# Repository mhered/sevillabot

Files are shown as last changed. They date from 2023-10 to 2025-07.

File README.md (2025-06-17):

# sevillabot
This is the repo for the team **sevillabot** of PiWars 2024 competition:
* [Quick Start Guide](./Quick-start-guide.md)
* [Shortcut Commands](./commands/README.md)
* [Bill of Materials](./BOM.md)
* [Activity Log](./activity_log.md)
* [Raspberry Pi setup (20.04 / Foxy)](./RPi_setup_foxy.md) or alternatively [22.0 / Humble](./RPi_setup_humble.md)
* [Motor wiring](./wiring.md)
* [Soldering Tips](./soldering.md)
* [Gamepad Controls](./gamepad_controls.md)
* [SLAM and Navigation](./SLAM_and_Navigation.md)
* [Line Follower](./Line_follower.md)
* [Simulation in gazebo](Simulation.md)
* [Inertia Properties](./inertial/Inertial.md) and [Center of Mass](./inertial/Weighing.md) estimation
* [Troubleshooting](Troubleshooting.md)
* [WIP](./WIP/) (some unfinished projects with improvements for next version of sevillabot):
  * [Menu](./WIP/menu/README.md): Adding an onboard interface
  * [RPi_zero](./WIP/RPi_zero/): moving from the RPi 4B to the RPi Zero 2 W
  * [IMU](./WIP/IMU/README.md): adding an IMU
* [Where are the large and private files?](./BKP_sevillabot/README.md)

Check out our [blog](https://sevillabot.blog).

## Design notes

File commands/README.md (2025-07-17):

# /commands/README.md
This folder contains bash commands to be used as shortcuts to interact with sevillabot. 

Open a terminal in this folder and launch commands. 

Each command opens a separate terminal.

Warning: this assumes the IP address of the robot has been already named `sevillabot`, see [Troubleshooting.md](../Troubleshooting.md) 

## Shortcuts for frequent remote commands in bot

| Usage | Commands sent to bot over SSH | Comments |
| --- | --- | --- |
| `$ . activate_bot.bash` | `$ cd ~/robot_ws`<br />`$ source install/setup.bash`<br />`$ ros2 launch sevillabot launch_robot.launch.py` | Spawns the robot. Sources ROS2 in the workspace then runs launch file that spawns the robot, launches twist_mux and joystick. |
| `$ . shutdown_bot.bash` | `$ sudo shutdown -h now` | Shuts down the RPi |
| `$ . miniterm.bash` | `$ miniterm` | Launches miniterm |
| `$ . camera.bash` | `$ cd ~/robot_ws`<br />`$ source install/setup.bash`<br />` $ ros2 launch sevillabot camera.launch.py` | Launches camera node |
| `$ . lidar.bash` | `$ cd ~/robot_ws`<br />`$ source install/setup.bash`<br />` $ ros2 launch sevillabot camera.launch.py` | Launches lidar node |

## Shortcuts for frequent commands in PC

| Usage | Commands executed in PC | Comments |
| --- | --- | --- |
| `$ . RVIZ.bash` | `$ rviz2 -d ~/dev_ws/src/sevillabot/config/bot_with_sensors.rviz` | Launches RVIZ with config file to view Lidar |
| `$ . view_image.bash` | `$ cd ~/dev_ws`<br />`$ source install/setup.bash`<br />` $ ros2 launch sevillabot camera.launch.py` | Launches RQT Image viewer |

## Sources

Inspired on this article: https://malcontentcomics.com/systemsboy/2006/07/send-remote-commands-via-ssh.html 
Check out this one too if need to send variables: https://malcontentcomics.com/systemsboy/2006/11/using-ssh-to-send-variables-in-scripts.html

Check this article for ways to launch several terminals or tabs with different titles: https://www.baeldung.com/linux/gui-open-terminals-run-commands

Check this article for ways to concatenate commands: https://unix.stackexchange.com/questions/159489/is-there-a-difference-between-and-and

Check this one for ways to avoid writing the password (e.g. for sudo commands?): [How to automate SSH login with password?](https://serverfault.com/questions/241588/how-to-automate-ssh-login-with-password)

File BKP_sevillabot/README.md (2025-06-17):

# README.md

A private backup of the following large and/or private files of the `sevillabot` project is uploaded to Dropbox:

* `Arduino/` - folder containing a backup of all Arduino `.ino` files in the white LG gram laptop (`gram` or Eve), just in case I forgot to save them in the repo (final ones should be in `code/` folder )
* `CAD`/ - folder containing the original CAD design of `sevillabot`, including FreeCAD files (all versions up to piwars and after, animated mechanisms, STL exports for 3D printing, etc), mega4 design uploaded to GrabCAD, all CAD files downloaded

* `firmware_update/` - folder with the files needed to manually fix ubuntu Mate install in the RPi

* `SD_images/` folder contains images of the SD card in sevillabot, one with a clean ubuntu 20.04 + ROS foxy and the one with all software loaded, as used during the competition in piwars2024

* `secrets.md` - login/pwd of sevillabot blog, email and twitter, wordpress recovery key, etc

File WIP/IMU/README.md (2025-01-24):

# Playing with an IMU

## Sources

- [Arduino Guide for MPU-6050 Accelerometer and Gyroscope | Random Nerd Tutorials](https://randomnerdtutorials.com/arduino-mpu-6050-accelerometer-gyroscope/)

A basic tutorial to get started with the MPU-6050 IMU and Arduino. Describes connections, provides Arduino code to get readings of accelerations and temperature

- [GitHub - hiwad-aziz/ros2_mpu6050_driver: A ROS2 package that interfaces with an MPU6050 sensor over I2C.](https://github.com/hiwad-aziz/ros2_mpu6050_driver)

A ROS2 driver for MPU-6050 IMU. I arrived originally to the fork by JosefGst, but there are plenty more and the one by hiwad-aziz seems to be the original one,. Explore the [forks](https://github.com/hiwad-aziz/ros2_mpu6050_driver/forks) to look for recently active ones. Zerobotics seems linked to Enzo Ghisoni

- [@ros2jsguy/mpu6050-motion-data - npm](https://www.npmjs.com/package/@ros2jsguy/mpu6050-motion-data/v/0.2.0)

Another MPU-6050 driver writtn in Typescrit 

- [Lessons learned while working with IMU Sensor, ROS2 and Raspberry Pi | by RoboFoundry | Medium](https://robofoundry.medium.com/lessons-learned-while-working-with-imu-sensor-ros2-and-raspberry-pi-a4fec18a7c7)

Comparison MPU6050 vs BNO055 (with magnetometer), calibration. There are more articles in the series.

Series of 3 Youtube vides by NeroCode. I saved local copies with subtitles to watch offline in [./videos_IMU_local](./videos_IMU_local):

- [(222) Control Robot Móvil Diferencial con ROS con Odometría | DESDE CERO | Parte 1 - YouTube](https://www.youtube.com/watch?v=1Ch-gtxvxyA)
- [(222) Cómo publicar datos de IMU MPU6050 usando ROS | Parte 2 - YouTube](https://www.youtube.com/watch?v=TaHY4OYBNwc&t=18s)
- [(222) Fusión de datos de IMU y Odometría de encoders mediante ROBOT_LOCALIZATION en ROS | Parte 3 - YouTube](https://www.youtube.com/watch?v=OopVfPZ2_ig)

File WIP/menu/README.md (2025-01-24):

# README.md

Miniproject to create a minimal interface aboard the robot.

Components:

* KY40 rotary encoder with switch
* SS1306 0.96" OLED display screen
* 3D printed parts

## 3D printed parts

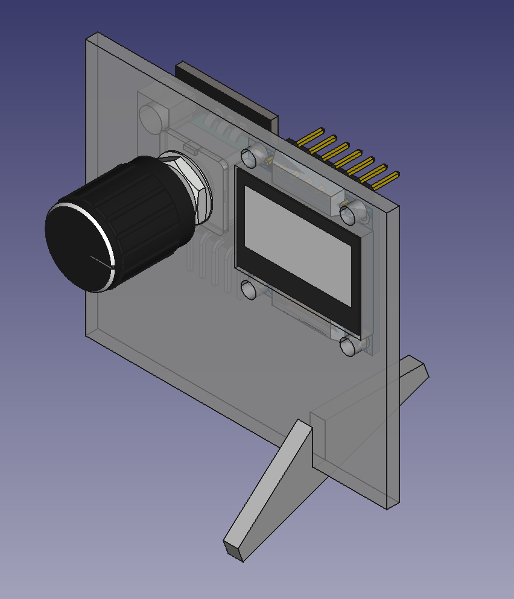
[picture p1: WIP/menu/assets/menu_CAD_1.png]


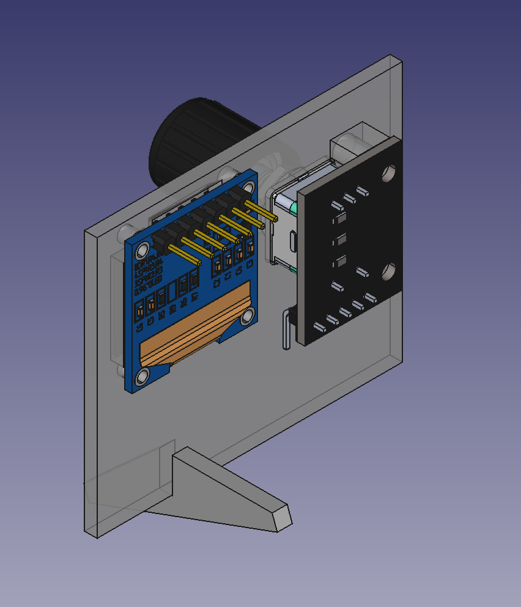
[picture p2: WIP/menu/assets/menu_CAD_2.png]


I downloaded CAD files of the components to aid the design, then fine tuned with physical measurements. Notes about the downloaded CAD files:

- `rotary-encoder-with-knop-1.snapshot.1`: downloaded as SLDPRT, converted to STEP using OnShape, OK!
- `oled-0-96-display-1.snapshot.1`: downloaded as STEP and OK(-ish, dimensions are a bit off and 6 pins instead of 4)
- `ky-040-rotary-encoder-1.snapshot.1`: downloaded as SLDPRT, converted to STL in AnyConv: KO, wrong scale!!
- `display-oled-ssd1306-de-0-96-1.snapshot.6`: downloaded as STEP but KO, dimensions not fitting part

Note: Some options for converting SLDPRT for free without SolidWorks:

* [AnyConv](https://anyconv.com/) but rather unreliable: scale not respected, or failure to convert 
* [ConvertCADFiles](https://convertcadfiles.com/): one free trial, afterwards pay per conversion
* Create account in [OnShape](https://cad.onshape.com/) (with SPAM user), open file then export as STL or STEP
* Not tested: [download eDrawing](https://www.solidworks.com/support/free-downloads) (for Windows)

## Arduino

### Wiring

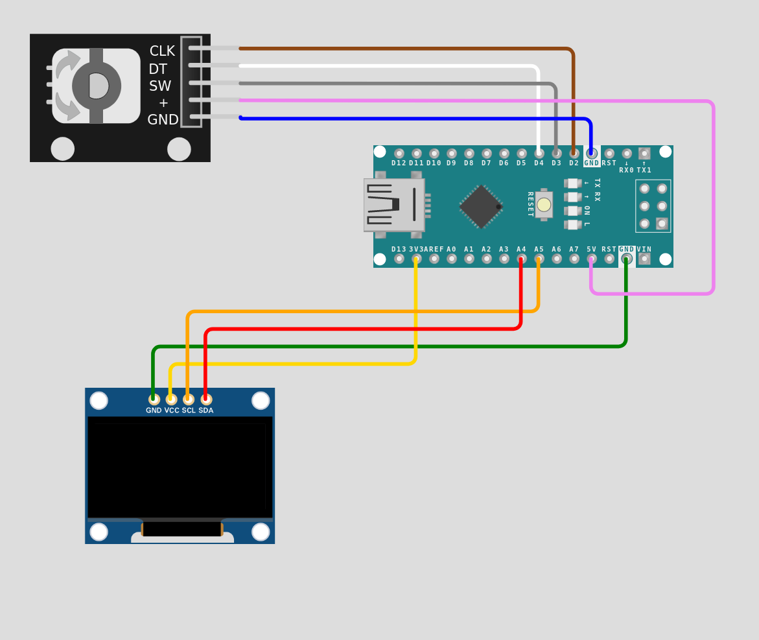
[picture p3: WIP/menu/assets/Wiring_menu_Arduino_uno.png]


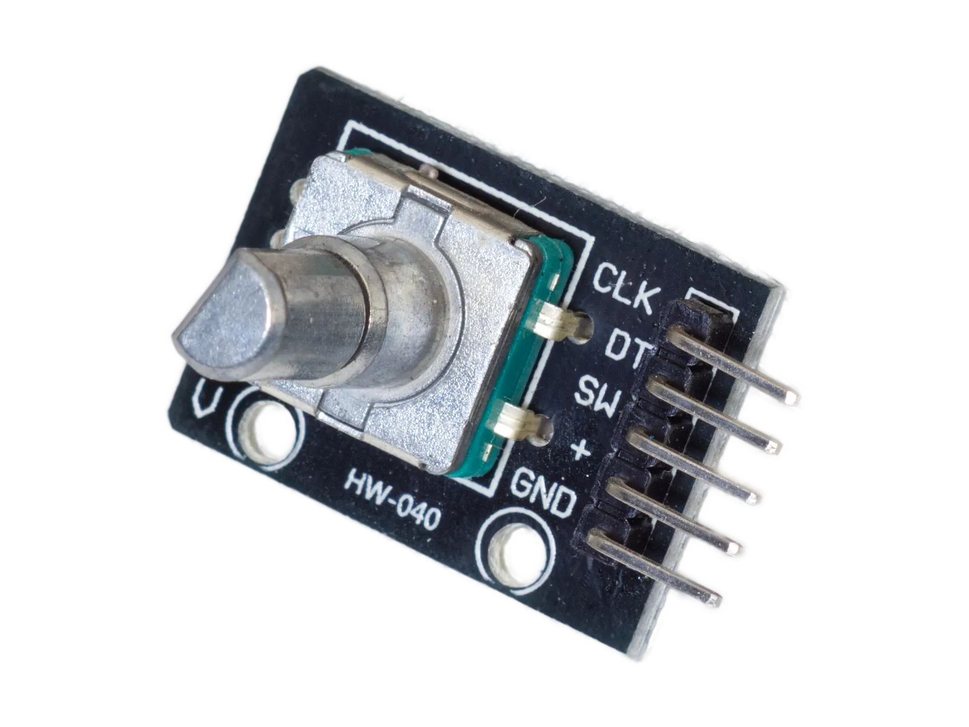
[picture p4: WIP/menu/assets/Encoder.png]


| KY-40 pin | Cable  | Arduino pin |
| --- | --- | --- |
| GND | blue | GND |
| + | purple | 5V |
| SW | grey | D3 |
| DT | white  | D4 |
| CLK | brown  | D2 |

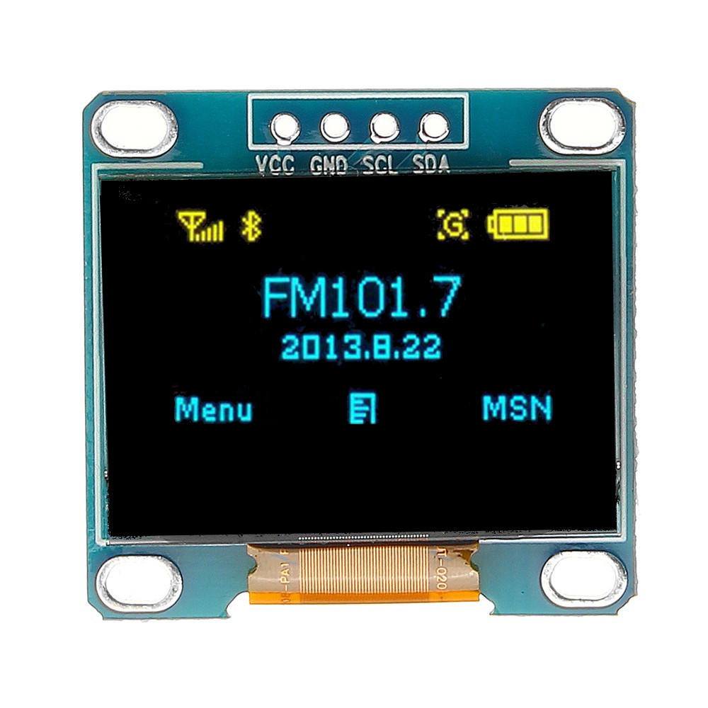
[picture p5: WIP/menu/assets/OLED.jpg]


| OLED pin | Cable  | Arduino pin |
| --- | --- | --- |
| GND | green  | GND |
| VCC | yellow | 3V3 |
| SCL | orange | A5 / SCL |
| SDA | red | A4 / SDA |

### Programming

#### Sources

* Inspired on the [video tutorial by upir ](https://www.youtube.com/watch?v=HVHVkKt-ldc) and [companion code](https://github.com/upiir/arduino_oled_menu/tree/main) for a beautiful menu design with icons for the OLED display. Note this code controls the menu using 3 push buttons. 

* I used ideas from this [video tutorial by LaBuhardillaDelLoco](https://youtu.be/cWgWvNhWg-A) and the [GFX library documentation](https://learn.adafruit.com/adafruit-gfx-graphics-library?view=all) to migrate to the Adafruit GFX and SSD1306 libraries for the OLED display,  instead of `u8g` (it was not working, although in hindsight it was probably due to wiring errors)

* Used ideas from this [video tutorial by Yvan from brainy-bits](https://www.youtube.com/watch?v=cYCTMdUi8P0 ) and its [companion blog post with code](https://www.brainy-bits.com/post/best-code-to-use-with-a-ky-040-rotary-encoder-let-s-find-out) on how to control a rotary encoder (with debouncing) to use it as input method
* Another [simpler menu with rotary encoder tutorial](https://www.youtube.com/watch?v=vHRyj3e3ZTU), which I didn't really use

* Created my own graphics online: used [Pixilart](https://www.pixilart.com/) which is super simple instead of [Photopea](https://www.photopea.com/) which is way more complex

* Convert images into C code arrays using online tool [image2cpp](http://javl.github.io/image2cpp/) 

* Test the sketch online using [WOKWI online emulator](https://wokwi.com/projects/397015999090347009) although it was not very practical with the OLED, had a tendency to trigger unexplained build errors when tweaking the appearance.

### Arduino sketch

Notes:

* Modified the Encoder code so it only registers clockwise or counterclockwise input when a full notch is moved (i.e. the knob fall in a stable position). Original code counted also halfway movements. 
* Encapsulated the code to control the encoder in a custom `Encoder` class. To include a class in arduino: add `#include "src/Encoder.h"` and put `Encoder.h` and `Encoder.cpp` files in a `/src/` subfolder below the location of the main `.ino` file, see [here](https://forum.arduino.cc/t/how-do-i-include-a-library-in-a-sketch-directory/1079812)
* I simplified a lot the code for the menu

### Issues / To Do

- [ ] The debouncing should not work because the wait time is almost 0! It was working when the only action is to print the command via serial (e.g. see `rotary_encoder_control_class.ino`)
- [ ] When the menu code is added to the mix, it fails sometimes to detect accurately the Encoder input, and behaves a bit erratically (e.g does not react or moves to the wrong selection ). Why?

- [ ] Encapsulate menu in a class

## Raspberry pi

Next step translate to use directly with RPi

See e.g. [this tutorial by Computadores y Sensores](https://www.youtube.com/watch?v=n0dHQSTSilM) which uses raspiOS, python and LUMA library. There are plenty of interesting examples reading info from the RPi system (e.g. date and time, network usage, temperature? )

#### Wiring

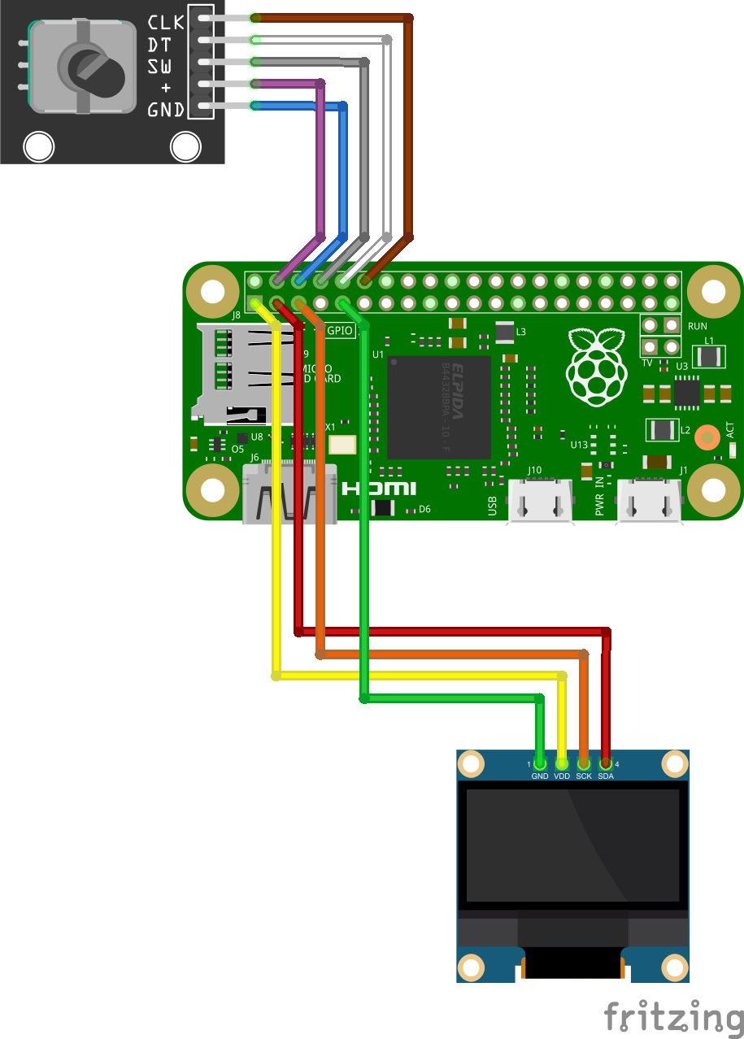
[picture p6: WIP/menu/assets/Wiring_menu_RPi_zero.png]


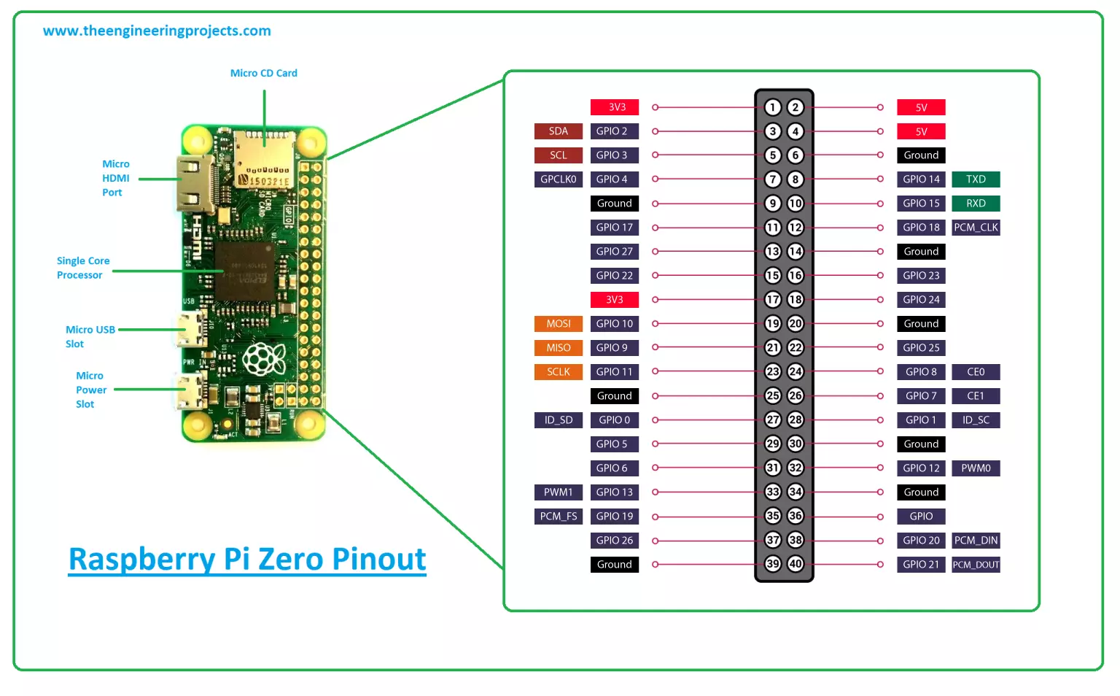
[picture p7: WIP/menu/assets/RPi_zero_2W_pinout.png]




| KY-40 pin | Cable  | RPi pin |
| --- | --- | --- |
| GND | blue | GND / #6 |
| + | purple | 5V / #4 |
| SW | grey | GPIO14 / #8  |
| DT | white  | GPIO15 / #10 |
| CLK | brown  | GPIO18 / #12 |



| OLED pin | Cable  | RPi pin |
| --- | --- | --- |
| GND | green  | GND / #9 |
| VCC | yellow | 3V3 / #1 |
| SCL | orange | GPIO 3 / SCL / #5 |
| SDA | red | GPIO 2 / SDA / #3 |

### Setup

I2C requires activation in Raspi, see this discussion: https://askubuntu.com/questions/1273700/enable-spi-and-i2c-on-ubuntu-20-04-raspberry-piNo but there is no need in ubuntu.

Install i2c-tools and check I2C devices are detected: 

```bash
sudo apt install i2c-tools
i2cdetect -y 1
     0  1  2  3  4  5  6  7  8  9  a  b  c  d  e  f
00:          03 -- -- -- -- -- -- -- -- -- -- -- -- 
10: -- -- -- -- -- -- -- -- -- -- -- -- -- -- -- -- 
20: -- -- -- -- -- -- -- -- -- -- -- -- -- -- -- -- 
30: -- -- -- -- -- -- -- -- -- -- -- -- -- -- -- -- 
40: -- -- -- -- -- -- -- -- -- -- -- -- -- -- -- -- 
50: -- -- -- -- -- -- -- -- -- -- -- -- -- -- -- -- 
60: -- -- -- -- -- -- -- -- -- -- -- -- -- -- -- -- 
70: -- -- -- -- -- -- -- --      
```

Install dependencies:

```bash
sudo apt-get install python3-dev python3-rpi.gpio
sudo apt install python3-pip
sudo pip3 install adafruit-circuitpython-ssd1306
```

Create a sample program

```python
from board import SCL, SDA
import busio
import adafruit_ssd1306

i2c =busio.I2C(SCL, SDA)

# create calss and define screen size

display = adafruit_ssd1306.SSD1306_I2C(128, 64, i2c)

#clear screeeb

display.fill(0)
display.show()

# define 1 pixel at the origin 0,0
display.pixel(0,0,1)

# define 1 pixel at center point
display.pixel(64,32,1)

# define 1 pixel at the opposite corner
display.pixel(127,63,1)

display.show()
```

It works!

#### Programming

#### Issues / To Do

- [ ] ssh onto the zero via USB: see this tutorial https://johnnymatthews.dev/blog/2021-02-06-connect-to-raspberry-pi-zero-over-usb-on-ubuntu/

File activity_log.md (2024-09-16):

# Made a blog in BlueHost

See secrets.md in local

# Made some logos

BrandCrowd (spam.mhered): https://www.brandcrowd.com/maker/shortlist/718945c4-b511-4b5e-aa74-6c4dfafddd57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

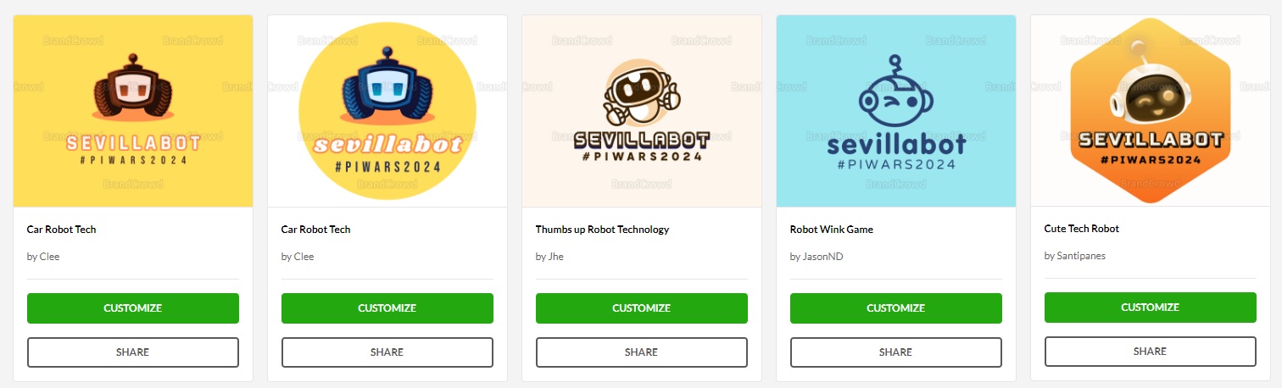
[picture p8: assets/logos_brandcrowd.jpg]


Looka.com: seems I didn't sign up and got assigned user: looka-ref-user-name-4GAHPhyn9S. Difficult to change the logo (need to scroll endlessly) 

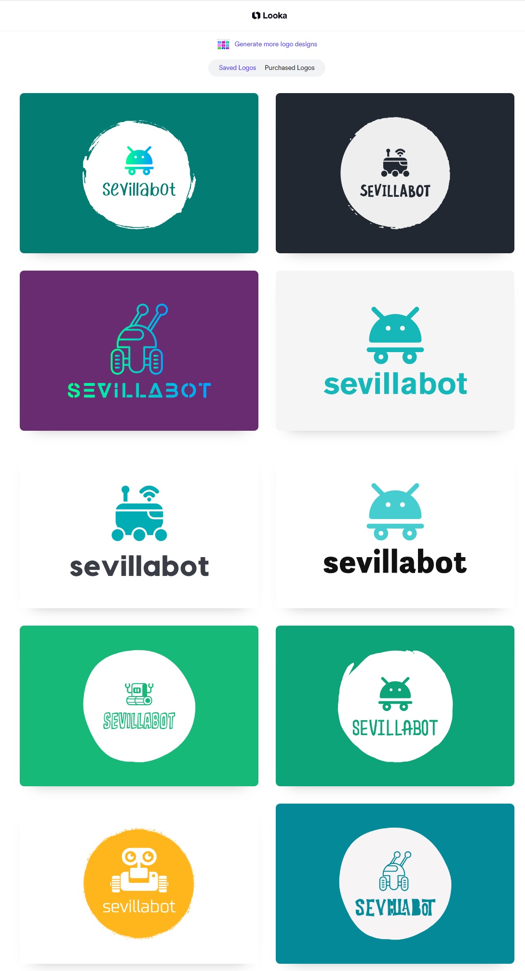
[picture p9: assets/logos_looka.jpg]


Temporary logo I chose for the blog:

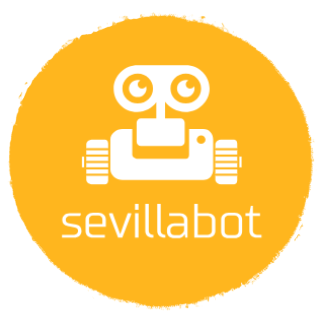
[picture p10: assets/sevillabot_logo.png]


# Ordered some items

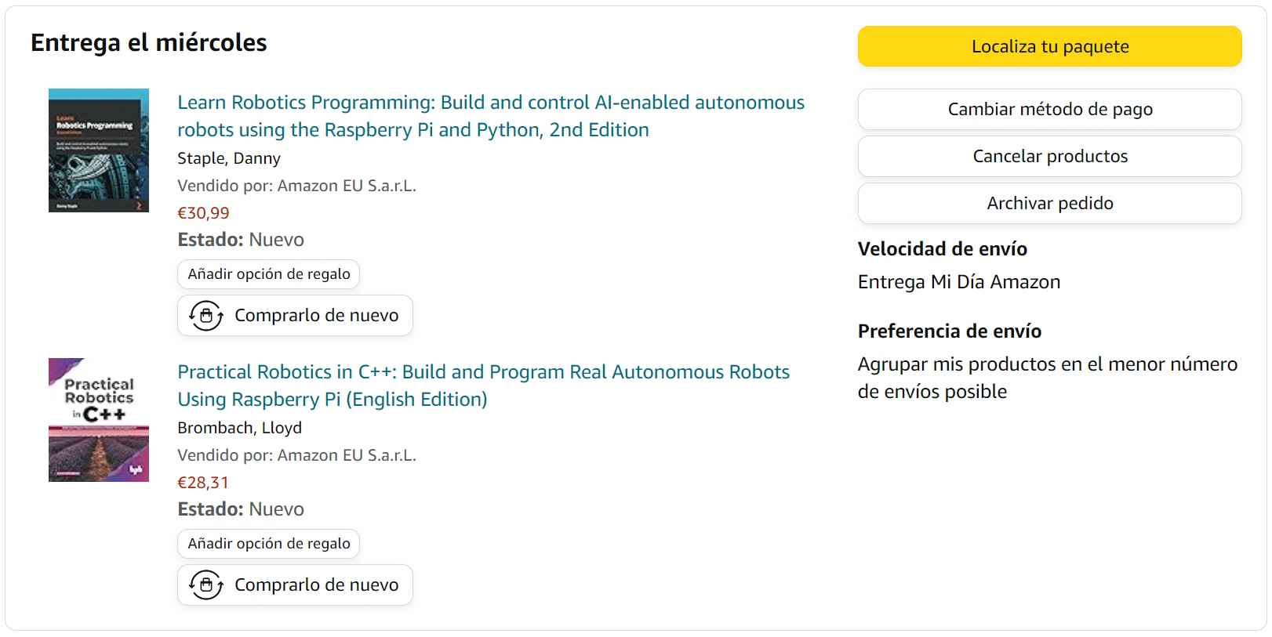
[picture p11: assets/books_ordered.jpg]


* Practical Robotics in C++ by Lloyd Brombach

* Learn Robotics Programming 2nd Ed by Danny Staple
* A Raspberry Pi 5
* 2x microUSB flat cables from Aliexpress (with a second account that uses Apple OAuth)
* Motors (x4), battery (x2), Arduino Nano (x3), and Buck converter (x3) all of them with some spares, from Amazon.

# Gathered references

Robofoundry resources: https://robofoundry.medium.com/

Checked out Simon robot: 

* https://esimonsite.com/proyectos/mini_robot/
* STEP file: https://github.com/simonllopez/mini_robot_hw/blob/c72156409fd8e69483608780fe5bce98770d15b5/Ensamblaje_Base_2023.step

# Notes on #piwars

38 Adults & Mixed teams will compete on 21st April in 3 categories: Beginner, Intermediate and Professional. **sevillabot** will compete in the category Beginner.

We make three commitments: 

- to build a robot to compete on the appropriate competition day.
- to provide regular updates, when requested, to assure that we are on track to complete our robot build and testing by the competition date. The organization will be setting deadlines for replies to ensure that spaces are not wasted, so **it is vital to respond to update requests** .
- to respond to (or acknowledge) all communications in a timely manner.

There is a fee of 20 GBP per team.

All teams must send at least one participant to the physical event in Cambridge. The maximum recommended team size is 10 people. The organization will ask how many members are actually attending to assign a suitable workroom onsite. All teams must have or be accompanied by a responsible adult. 

# Safety rules 

* In the workrooms all robots must remain powered down or ‘on blocks’ to prevent any remote control conflicts or autonomous mistakes may cause damage.
* Robots must not (intentionally) emit smoke or flames.
* No soldering within the building. Soldering is acceptable outside the building with a **battery-powered soldering iron**, taking care that no smoke enters the building and triggers the smoke detectors. 

# Robot rules

## One single robot

We are permitted to enter **one single robot** to the competition. This robot must handle all of the challenges. We are not permitted to *swap out* the entire robot at any time. It may have attachments, and we are permitted to exchange *parts* of our robot to compete in the different challenges (e.g. motors and wheels) but it must remain fundamentally the *same* robot: When adding attachments, the basic chassis, Raspberry Pi and controller arrangement must remain the same.

## With an official Raspberry Pi at the Core

We may use multiple Pis (Pi, Zero, Pico) and other boards (e.g. Arduinos, micro:bits, even non-official RP2040-derived boards, or other) BUT **an official Raspberry Pi board must be in overall/central control of your robot as the primary/core processor**. 

Additional pieces of equipment e.g. a games controller, a laptop, mobile phone or tablet may be used to control the robot, but **must not be physically attached when competing on the courses**.

## Battery-powered

All robots must be powered by batteries and must operate without being tethered to a static mains electricity power source.

Mains power may be used for recharging battery packs.

If LiPo batteries are used, **any charging must supervised and be done inside a fire-proof bag or box**

## Only some configurations are allowed

No airborne robots are permitted, e.g. drones.

Walking and self-balancing robots are permitted.

Hovercraft-style robots are allowed *provided that any fans are enclosed safely*.

## And robot dimensions are constrained

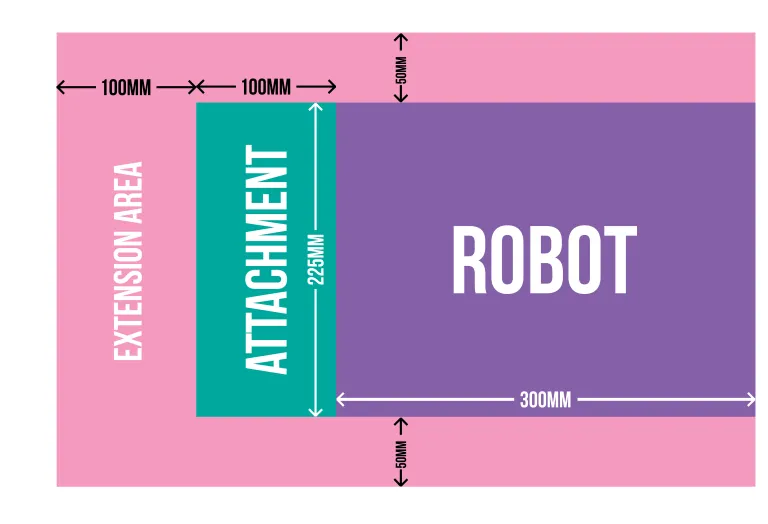
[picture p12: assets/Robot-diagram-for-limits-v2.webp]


### Main chassis

The main chassis (including wheels and any protrusions that form part of the main robot) of competing robots must fit within a 225mm width x 300mm length x 370mm height box (purple area)

### Attachments

Attachments may be added to the robot for specific challenges. Any attachment can add additional length of 100mm and height of 80mm (as in the green area in the diagram above) such that, when the attachment is at rest there is no additional width, maximum length must be no more than 400mm, the maximum height must be no more than 450mm.

An attachment may be *animated* in some way such that it extends beyond the boundaries above into the “extension area”. However, the attachment must stay within a box 325mm wide by 500mm length (this is shown as the pink area above).

## Our thoughts

The basic architecture of our current robot is in line with the rules, but we need to think about changing the chassis because the wheels are too wide apart and the camera protrudes too much at the front (although the camera could pass as an attachment maybe?).

Will need to adapt the dimensions of the current robot: 34cm long (ko by 4cm, would need to move front camera) x 27 cm wide (ko by 5.5cm, could fix moving wheels inwards because bottom width is 14cm and wheel width is 3cm, leaves 1cm clearance in each side and some to spare) x 24 cm high (ok)

Other changes: 

* should remove large screen (heavy and hungry)
* Castor wheels are not recommended. Consider 4WD mecanum? How to program mecanum wheels: https://www.youtube.com/watch?v=gnSW2QpkGXQ

# The Challenges

Each challenge can earn points that contribute to an overall score. None are mandatory but no points can be earned from challenges not entered.

## [Lava Palava](https://piwars.org/2024-disaster-zone/challenges/lava-palava/) - Escape the volcanic eruption

This challenge is autonomous-only: the Raspberry Pi will control the robot by itself for the entire duration of the challenge without interference from the operator, except for a button press to initiate movement and another, if necessary, to stop movement.

This will require a line-following algorithm. I think there are specific line-detection sensors, otherwise I could use a camera. Potentially I could use a Lidar to stay away from the walls.

4/1 We bought a line sensor, built a support and tested the sensor on a black line over white background. It was not very robust, perhaps related to calibration with direct light and shadows? We need to modify the code to detect a white line over black background. Also, need to add a PID, but I need a working robot base to calibrate the gains and test it!

1/2 checking dimensions to mock-up the arena for testing: 7m long course, 570mm long by 53mm high speed bump, section is channel 550mm wide with 70mm high walls (even in speed bump), painted black with 19mm wide white centre line. There are 2 turns, looking at the sketch the turns are approx 780mm long at 45 degrees. Robot must cross finish line. Need start/stop button. Retrieve manually from end of course. 3 runs. Apparently in the documentation: https://www.pololu.com/docs/0J18/17 there is a `read_line_white()` function.

## [Eco-Disaster](https://piwars.org/2024-disaster-zone/challenges/eco-disaster/)- Sort the barrels of toxic waste!

### Challenge description

This challenge can be driven autonomously *or* by remote control. The points available are weighted so autonomous robots can earn more points.

### Our thoughts

1/1 Finished the first working prototype of a beautiful clamp actuated by a stepper motor. Need to have a working base robot to be able to test it.

## [Escape Route](https://piwars.org/2024-disaster-zone/challenges/escape-route/) - Navigate the blind maze to find your way out!

### Challenge description

The arena for the maze is made of a by a 2m by 3m area surrounded by a 119mm high walls, all painted in matte black. There are 3 colored blocks (red, green, blue) are placed as obstacles in any one of six predefined configurations, unknown in advance.

There are three ways to compete in this challenge (The points available are weighted so autonomous robots can earn more points):

* **Fully autonomous**: The team has 1' to calibrate the vision system then can only press start and stop.
* **Blind remote control**: Teleoperated via sensora on the robot and a screen for the driver.
* **Call and response**: With a team member looking at the maze and giving instructions to a driver who cannot see the maze

### Our thoughts

I am thinking going for blind remote control if I can position the lidar below 119mm. For this one I need to build a replica of the maze and practice a lot!

## [Minesweeper](https://piwars.org/2024-disaster-zone/challenges/minesweeper/) -  Find and defuse the bombs!

### Challenge description

Arena: 1.6 by 1.6m area surrounded by 30cm tall black walls. The floor is made of 4x4 squares of white opaque perspex.

A single, random square will be lit up in red. The robot must visit the  square in question and stop, motionless for 1 second with some part of  the robot over the square. The light goes off and another random tile lights up up to 20 times.

Autonomous teams will have 1' to calibrate the vision system.

This challenge can be driven autonomously or by remote control. The points available are weighted so autonomous robots can earn more points.

### Our thoughts

I can imagine some vision system based on a top mounted camera, then a routine that turns the robot until the light is in front of the robot, then moves towards it, stops when it is on top of it, then waits 1", then repeats when a .

Mocking somewhere to test to fine tune (field of view, detecting light, when to stop etc) may be difficult though. I think we may compete here with remote control.

11/12 - check out this very nice blog:https://eastdevonpirates.blogspot.com/2023/12/minesweeper-piwars-2024.html with a discussion.

Found 30cm 130 degree convex mirrors in Amazon for 30€. Made some calculations and with a picamera (75degrees angle of view) placed at 10cm from the floor looking upwards, the convex mirror placed 20cm above the camera facing downwards I could monitor a circle 154cm in diameter. But the mirror weighs 1kg...

## [The Zombie Apocalypse](https://piwars.org/2024-disaster-zone/challenges/zombies/) - Shoot the undead!

### Challenge description

The robot is placed 1- 1.5m away from a tower with 3 levels: ground, middle and top floor up to 60cm above ground. The aim is to hit card-sized targets (62mm by 88mm) using balls or Nerf projectiles.

This challenge can be driven autonomously *or* by remote control. The points available are weighted so autonomous robots can earn more points.

However, as there uncertainty about the exact distance and the geometry of the tower, we don't know really how to identify the targets automatically. By color? Some specific design? Generally, we have questions about this challenge. What are targets in the "compound"? 

### Our thoughts

Today (19/10) I bought a [laser pointer]() and a [Nerf](). I am thinking about attaching the nerf and adding some servos to aim up and down, pull the trigger of the Nerf and reload it. Also I could imagine some way of auto aiming by detecting the laser with a camera, but I don't really know how to choose the target automatically.

11/12 - check out new information released in the discord and the official website with details of the arena and the design of the zombies

24/1 We made a beautiful prototype gun that employs 3D printed structural parts, a car door lock actuator to pull the trigger and a stepper motor to aim the gun in pitch. In order to increase precision and reduce torque, we used a pulley system with a small gear and a large gear.

Observations from the first test of the prototype in a mock-up arena for the zombie challenge:

* The completed gun assembly fits within 400mm long x 200mm wide x 200 mm high box, which should be ok.
* We need to balance the gun: the axle is too far forward. Since there is not much room to move the axis backwards, this can be compensated instead adding weight at the front of the gun (two tape rolls on top of the laser pointer made the trick). Without this, the stepper motor does not really have enough torque to lower the gun and aim lower
* There is not enough clearance between the trigger mechanism and the supports or the robot base for the pitch angle range to reach the higher positions at the top of the 60cm high target area, specially from the closest 1m distance. We need to redesign the supports to make them at least 40mm higher and give them more angle so the attachment of the supports to the robot moves forward at least 30mm. This may cause FreeCAD to break....  
* The pulley system does not appear robust. At times it seems to hesitate or skip teeth, perhaps the stepper is lacking torque and/or the belt is not tight enough. Although applying the stepper directly to the axis may provide sufficient precision, this requires more torque... maybe try the NEMA stepper without the pulley system?

28/1 - Progress:

* Realised it may be sufficient to move supports apart so they don't clash with the trigger mechanism.
* Modified supports: 30 mm higher, replaced clamp with clip-on system to secure bearing in place. Issue: Pending testing, RH support seems flimsy and may require reinforcement.
* Modified 3D printed parts `gun_holder` to move axle backwards, `trigger_support` to clear the battery compartment, plus made RH and LH to make assembly narrower
* Realised jammings can be solved from the cartridge compartment, no need to access the other door
* Installed all elements temporarily on the robot base (battery, fuse, power rail, arduino, motor driver, relay, door lock actuator) 
* Implemented basic keyboard control to aim the gun, toggle the laser and to fire the trigger.  Keyboard control works with python script `command_gun.py` running in the computer. Issues: `keyboard` library requires `sudo`, need to manually set in the code the port in which Arduino is connected. One keyboard press some times fires several shots in quick succession. 
* Tested NEMA17 motor with L298N driver and arduino. May not have enough resolution: 200 steps means 1.8 degrees resolution means 47mm steps at 1.5m! 

## [Pi Noon - The Hindenburg Disaster](https://piwars.org/2024-disaster-zone/challenges/pi-noon/) - Defend your balloon from an explosive end!

One (or more) members of the team will control the robot via wireless controller(s). This challenge *could* be tackled autonomously for the laughs, without extra points.

24/1 still waiting for the block

29/1 Delivery failed because 5€ worth of taxes were due... Will need to pick it up from the post office.

## [The Temple of Doom](https://piwars.org/2024-disaster-zone/challenges/temple-of-doom/) - Go on an adventure and tackle the obstacles in your way!

This is a remote-controlled challenge to test the agility of our robot and our driving skills. The obstacle course will only be revealed on the day of the competition, so it is important to watch the competition on Saturday. 

Not a lot of information, we just know that the course contains "several fiendish traps, snags and puzzles", and some recommendations from the organization of robot features that may help: 

* low center of gravity
* good ground clearance
* good grip
* power to drive up slopes

All obstacles **must** be *attempted* first, then we may skip them (but no points for skipped obstacles). We have up to **three attemps** at the challenge within the 5' time limit.

### Ideas to improve wheel grip

* Add weight to the robot
* moving the CoG above the wheel axis (away from the caster)
* Add rubber additive / liquid latex?

# Opportunities for more points

- [**Blogging Challenge**](https://piwars.org/2024-disaster-zone/challenges/blogging/) – Describe our **pre-event** exploits in words, videos and/or photographs. [See some hints here](https://piwars.org/blogging-challenge-guidelines/). Up to 1400 points per robot.
- [**Technical & Artistic Merit**](https://piwars.org/2024-disaster-zone/challenges/technical-and-artistic-merit/) – **record a video up to 5' in length** and **submit it ahead of the competition** to document the robot's Technical Merit (features, build quality and other technical aspects) and the design and artistic features (Artistic Merit). Videos will be scored by expert judges ahead of the competition. Up to 2800 points per robot.
- **Most Disastrous Robot Special Award** – to the robot that has the design most influenced by the Disaster theme (natural, man-made, movie-style disasters, or a combination, responses to disaster such as rescue vehicles etc. Up to 700 points per robot.

## Resources

* Cool Piwars blogroll: https://philipmcgaw.com/piwars-blogroll/

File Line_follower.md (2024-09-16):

# Line Follower

## Setup

### Custom messages

1. Create a `/msg` folder and declare custom message `TimestampedData.msg`

```
int64 timestamp
int32 data
```

2. modify `CMakeLists.txt`:

```python
...
# find dependencies
find_package(rosidl_default_generators REQUIRED)

# Declare ROS2 interface files
rosidl_generate_interfaces(${PROJECT_NAME}
  msg/TimestampedData.msg
  DEPENDENCIES std_msgs
)

# Export dependencies
ament_export_dependencies(rosidl_default_runtime)
...
```

3. modify `package.xml`

```xml
  <buildtool_depend>rosidl_default_generators</buildtool_depend>
  ...
  <exec_depend>rosidl_default_runtime</exec_depend>
  <member_of_group>rosidl_interface_packages</member_of_group>

```

4. compile, source and check it is available

```bash
$ colcon build --symlink-install
$ source install/setup.bash
$ ros2 interface list | grep sevillabot
    sevillabot/msg/TimestampedData
```

Note: For some reason when the node is called from normal terminal it freezes and publishes always the same value:

```bash
$ ros2 run sevillabot line_follower_publisher.py
$ # or
$ python3 ./src/sevillabot/my_scripts/line_follower_publisher.py
```

I need to call it from vs_code terminal, and after that it runs well... why? 

## Quick Start Guide for Gazebo

Plug the line follower add-on

Launch  publisher, PID, gazebo, RVIZ and twist_mux

```bash
(in VSCODE Terminal!!)$ ros2 run sevillabot line_follower_publisher.py 

(PC T1)$ ros2 run sevillabot pid.py 

(PC T2)$ ros2 launch sevillabot launch_sim.launch.py world:=~/dev_ws/src/sevillabot/worlds/obstacles.world

(PC T3)$ rviz2 -d ~/dev_ws/src/sevillabot/config/slam_gazebo.rviz

(PC T4)$ ros2 run twist_mux twist_mux --ros-args --params-file ~/dev_ws/src/sevillabot/config/twist_mux.yaml -r cmd_vel_out:=diff_cont/cmd_vel_unstamped

```

When moving the sensor away from the line the robot turns to counter the error!!

## Quick Start Guide Robot

### Launch the robot

Currently requires three calls, each of which requires to ssh into sevillabot, `cd ~/robot_ws`, `source install/setup.bash`. I should combine these three in a single launch file.

```bash
(bot T1)$ ros2 launch sevillabot launch_robot.launch.py # launch robot

(bot T2)$ ros2 launch sevillabot joystick.launch.py # launch gamepad

(bot T3)$ ros2 run twist_mux twist_mux --ros-args --params-file ~/robot_ws/src/sevillabot/config/twist_mux.yaml -r cmd_vel_out:=diff_cont/cmd_vel_unstamped # launch twist_mux
```

After modifying robot_launch, the three calls no longer necessary:

```bash
(bot T1)$ ros2 launch sevillabot launch_robot.launch.py # launch robot, gamepad & twist_mux
```

Equivalent to the shortcut:

```bash
(PC)$ cd sevillabot/commands/
(PC)$ . activate_bot.bash
```

### Launch the subscriber

I don't know yet why the subscriber is not launching properly but found a hack that works:

1. miniterm onto Arduino. Note this triggers calibration (2 solid LED in Arduino) and it takes a little while before it starts publishing data. Move around the sensor in and out the line during the calibration period, otherwise data will not be reliable later. When calibration finishes, LEDs in the Arduino start blinking.

```bash
(bot T4)$ miniterm 

--- Available ports:
---  1: /dev/ttyAMA0         'ttyAMA0'
---  2: /dev/ttyUSB0         'USB2.0-Ser!'
---  3: /dev/ttyUSB1         'USB2.0-Ser!'
--- Enter port index or full name: 3

E:12568	3500 #frozen during calibration
E:12568	3500
E:12568	3500
E:12568	3500
....
E:16367	3500 # then starts transmitting
E:16620	3501
E:16873	3502
E:17127	3498
E:17380	3499
E:17633	3505
```

2. launch the node in another terminal

```bash
(bot T5)$ ros2 run sevillabot line_follower_publisher.py 
```

3. close miniterm in the previous terminal with `CTRL + ]`. This somehow wakes up the node and it starts publishing. 

```bash
(bot T4)$ # exit miniterm with CTRL + ] : hack to get line_follower_publisher.py to publish!!
```

### Launch the PID node

Warning: put the robot on blocks because soon as you launch this node the robot starts moving. 

We can reuse Terminal 4 after closing miniterm

```bash
(PC T4)$ ros2 launch sevillabot pid.launch.py 
```

The advantage of using the launch file instead of running the node directly (`ros2 run sevillabot pid_node.py`) is that the launch file reads the PID gains and linear speed from the YAML file line_follower_pid.yaml. An example that works for speed = 0.1:

```yaml
line_follower_controller:
  ros__parameters:
    Kp: 20.0
    Ki: 0.0
    Kd: 2.0
    linear_vel: 0.1
```

For 0.15:

```yaml
line_follower_controller:
  ros__parameters:
    Kp: 30.0
    Ki: 0.0
    Kd: 3.0
    linear_vel: 0.15
```

You can modify the parameters in the file and relaunch the node without the need for recompiling.

After modifying the distance between wheels the above parameters don't work anymore.

An example that works for speed = 0.1 (with wheels @ 225mm instead of 275)

```yaml
line_follower_controller:
  ros__parameters:
    Kp: 15.0
    Ki: 0.0
    Kd: 0.0
    linear_vel: 0.1
```

## Quick Start Guide Line Follower with shortcuts

```bash
$ . activate_bot.bash # spawn bot
$ . miniterm.bash # launch miniterm
$ . line_sensor.bash # launch line_sensor subscriber. Close miniterm to activate it
$ . pid.bash # launch PID to start moving
```

## To do

- [ ] Understand and fix why the `line_follower_publisher.py` node only works when launched from vs_code terminal (??) -> Seems related to serial communication. Opening and closing miniterm seems to work as well.
- [x] modify `pid_node.py` to read PID constants and linear speed from `line_follower_pid.yaml` -> this will simplify fine tuning Done 11/04/24
- [x] integrate gamepad and twist_mux in the robot launch file `launch_robot.launch.py` -> this will simplify launching! DONE 13/04/24
- [ ] maybe try to integrate also `line_follower_publisher.py` and `pid.py` in a `launch_follower.launch.py`, this will simplify launching, and may fix the issue with serial!

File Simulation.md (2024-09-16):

# Simulation

## Quick start

1. Spawn the robot

```bash
$ cd ~/dev_ws/
$ source install/setup.bash
$ ros2 launch sevillabot rsp.launch.py use_sim_time:=true
```

2. Launch gazebo

```bash
$ cd ~/dev_ws/
$ source install/setup.bash
$ ros2 launch sevillabot launch_sim.launch.py
```

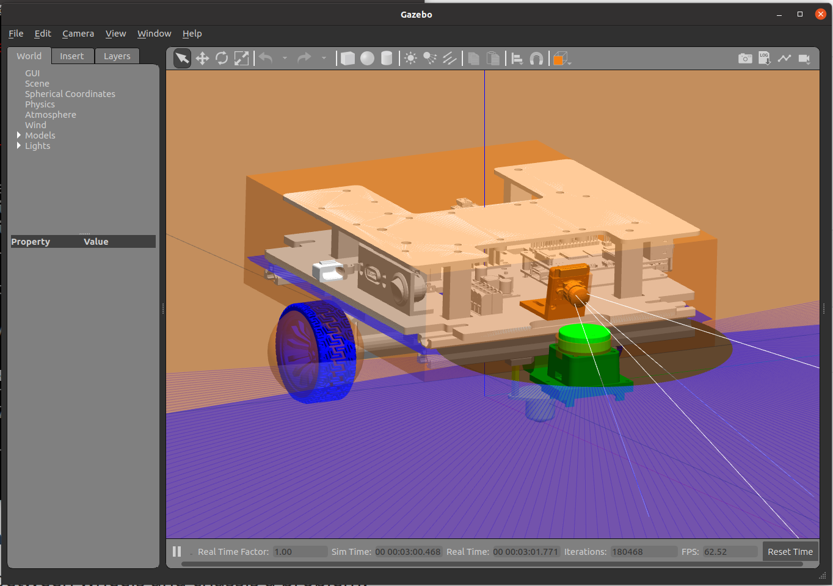
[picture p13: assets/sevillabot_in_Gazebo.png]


3. Display in RVIZ

```bash
$ cd ~/dev_ws/
$ source install/setup.bash
$ ros2 launch sevillabot display.launch.py
```

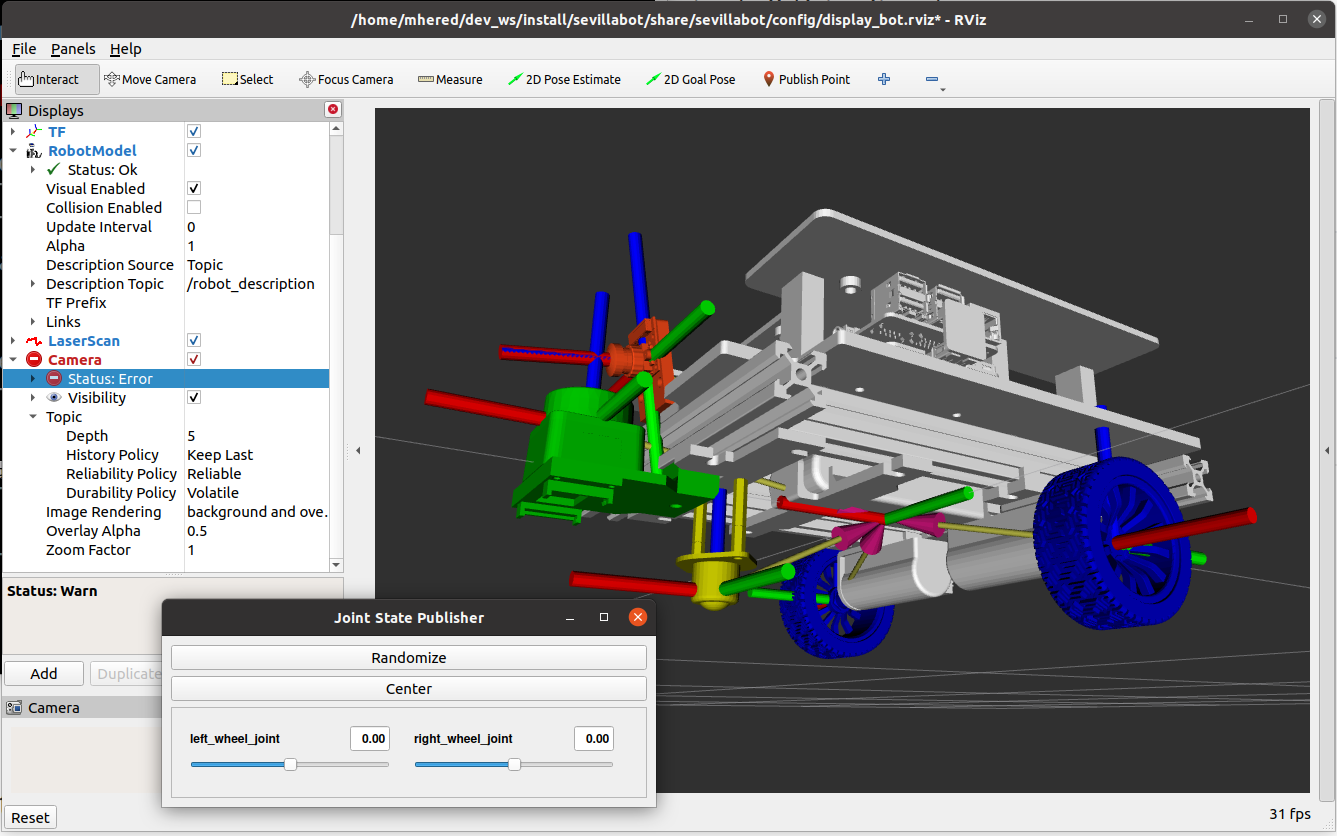
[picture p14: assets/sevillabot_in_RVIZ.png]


4. Teleop with keyboard

```bash
$ cd ~/dev_ws/
$ source install/setup.bash
$ ros2 run teleop_twist_keyboard teleop_twist_keyboard
```

or,  Teleop with gamepad (plugged to PC)

```bash
$ cd ~/dev_ws/
$ source install/setup.bash
$ ros2 launch sevillabot joystick.launch.py
```

## Exporting a FreeCAD assembly to STL

Issue: Body placement is not respected when exporting an assembly as STL.
Workaround (see https://github.com/FreeCAD/FreeCAD/issues/12278):

1. Move all the items you want to export to a Part
2. Go to the Mesh Workbench
3. Create a Mesh from the Part
4. Export those meshes as STL

To maintain local origin, copy the Part to root axes then export this copy of the part.

Issue: cannot export to DAE format (missing pycollada error message)

## Adding a mesh to URDF

Place meshes in `meshes` folder, modify to `CMakeLists.txt` to install this directory 

Use `filename="file://$(find sevillabot)/..."` for path

Note: need to scale when importing (FreeCAD units are mm, Gazebo units are m)

```xml
<mesh filename="file://$(find sevillabot)/meshes/ASSY_sevillabot_base.stl" scale="1.0e-3 1.0e-3 1.0e-3"/>
```

## Fine tuning

* In `properties.xacro` fix `W_z` (wheel axis z-offset in m) = 0.02 (not 0.025, otherwise wheels are out of their axes!) Checked it matches FreeCAD reference frame displacement.
* modified `launch_sim.launch.py`to load `sevillabot_world.world` as default world for gazebo simulation
* Added default RVIZ config `display_bot.rviz`
* In `camera.xacro` modify horizontal FOV to 160 degrees. Since camera is small, remove <collision> and <inertial> tags. 
* Update `Camera.md` with camera properties
* in `Simulation.md` add notes for teleop with joystick and all changes above

## To Do

- [x] add wheels mesh
- [x] add caster mesh
- [x] align height of caster
- [x] measure and correct position of wheels
- [x] is collision between wheels and chassis a problem? Apparently not
- [x] adjust angle of lidar
- [ ] measure values of CoGs, masses, inertias and update in URDF

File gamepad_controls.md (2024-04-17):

## Connect gamepad directly to the robot

We bought the Logitech 710 with a USB dongle. Allows running `/joy_node` from the bot, less lag, no need to carry the laptop around.

## Write a Python node to monitor `/joy` topic and send commands to the Arduino 

I wrote  [joy_subscriber.py](./sevillabot/scripts/joy_subscriber.py)

To get a mapping of your gamepad:

```bash
(T1):$ ros2 run joy joy_node
(T2):$ ros2 topic echo /joy
```

The Logitech 710 has two modes: X and D.  Instructions recommend mode X but the mapping seems strange. Note for example Left joystick only has discrete values in mode X.
Note also that MODE and VIBRATION do not trigger any response in `/joy` topic

| | Mode X | Mode D |
| --- | --- | --- |
| buttons[0]  | A | X |
| buttons[1]  | B | A |
| buttons[2]  | X | B |
| buttons[3]  | Y | Y |
| buttons[4]  | LB | LB |
| buttons[5]  | RB | RB |
| buttons[6]  | BACK | LT |
| buttons[7]  | START | RT |
| buttons[8]  | ? | BACK |
| buttons[9]  | Left Stick Push on | START |
| buttons[10] | Right Stick Push on | Left Stick Push on |
| buttons[11] | | Right Stick Push on |
| axes[0] | Cross Left/Right. Discrete values Left= +1. None = 0, Right = -1 | Left Stick Left/Right. Float values from +1 (Left) to -1 (Right) |
| axes[1] | Cross Up/Down. Discrete values Up = +1, None = 0, Down = -1  | Left Stick Up/Down. Float values from +1 (Up) to -1 (Down) |
| axes[2] | LT. Float values from +1 (Not pressed) to -1 (Fully pressed) | Right Stick Left/Right. Float values from +1 (Left) to -1 (Right) |
| axes[3] | Right Stick Left/Right. Float values from +1 (Left) to -1 (Right) | Right Stick Up/Down. Float values from +1 (Up) to -1 (Down)  |
| axes[4] | Right Stick Up/Down. Float values from +1 (Up) to -1 (Down)  | Cross Left/Right. Discrete values Left= +1. None = 0, Right = -1 |
| axes[5] | RT. Float values from +1 (Not pressed) to -1 (Fully pressed) | Cross Up/Down. Discrete values Up = +1, None = 0, Down = -1  |
| axes[6] | Left Stick Left/Right. Discrete values Left= +1. None = 0, Right = -1 | |
| axes[7] | Left Stick Up/Down. Discrete values Up = +1, None = 0, Down = -1 | |

## Fix the project to compile the node `joy_subscriber.py`. 

I found the fix here:
https://answers.ros.org/question/299269/ros2-run-python-executable-not-found/

- Add the Python source file to `sevillabot/scripts`
- Add an empty `__init__.py` file in the folder `sevillabot/scripts`
- Make sure the file is executable with `chmod +x joy_subscriber.py`

- Make sure the first line of code is the python shebang:  `#!/usr/bin/env python3`
- In `CMakeLists.txt`:

> ```
> # Install Python executables
> ament_python_install_package(scripts)
> 
> ...
> 
> install(
> 	PROGRAMS scripts/joy_subscriber.py  
>   	DESTINATION lib/${PROJECT_NAME} 
>   )
> ```

Apparently mixing CPP and python in a package is a big deal, see more details here:
https://roboticsbackend.com/ros2-package-for-both-python-and-cpp-nodes/

Not sure how I got it to work the first time but I am pretty sure I didnt add the `install ( PROGRAMS...` part.

To compile:

```bash
$ cd ~/robot_ws
$ colcon build --symlink-install 
$ source install/setup.bash
```

## Quick start

To run you need to open several ssh terminals, source and run different nodes:

```bash
(bot1):$ ros2 launch sevillabot launch_robot.launch.py # spawns bot
(bot2):$ ros2 launch sevillabot joystick.launch.py # launches joy_node and teleop_node with params and remapping of cmd_vel
(bot3):$ ros2 run sevillabot joy_subscriber.py # launch joy_subscriber
```

## Note on unique Arduino addresses

`/dev/ttyUSB*` depends of plugging order

`/dev/serial/by-id/*` is supposedly an unique ID but all my Arduino nanos share the same!: `/dev/serial/by-id/usb-1a86_USB2.0-Ser_-if00-port0`

`/dev/serial/by-path/*` depends on where the device is physically connected  (which USB port). Could work if we assign dedicated USB ports to specific Arduinos and are consistent with it.

| RPi4 USB port position | `/dev/serial/by-path/*` address of Arduino nano |
| -- | -- |
| top right | `/dev/serial/by-path/platform-fd500000.pcie-pci-0000:01:00.0-usb-0:1.1:1.0-port0` |
| bottom right | `/dev/serial/by-path/platform-fd500000.pcie-pci-0000:01:00.0-usb-0:1.2:1.0-port0` |
| top right | `/dev/serial/by-path/platform-fd500000.pcie-pci-0000:01:00.0-usb-0:1.3:1.0-port0` |
| bottom left | `/dev/serial/by-path/platform-fd500000.pcie-pci-0000:01:00.0-usb-0:1.4:1.0-port0` |

Found using:

```bash
$ ls -l /dev/ttyUSB* # detects serial devices
$ udevadm info /dev/ttyUSB0 # gets info for each device
```

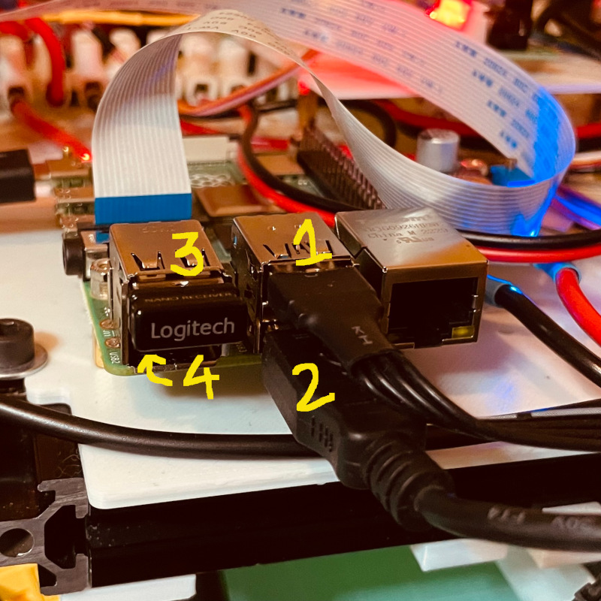
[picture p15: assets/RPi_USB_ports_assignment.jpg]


Assignment of sevillabot USB ports: Arduino for Base robot in 1, Addon Arduino in 2, Gamepad dongle in 3, 4 is spare

Modified both [ros2_control.xacro](./sevillabot/description/ros2_control.xacro) and [joy_subscriber.py](./sevillabot/scripts/joy_subscriber.py) to use  `/dev/serial/by-path/*` instead of `/dev/ttyUSB*` or `/dev/serial/by-id/*`

And now it works!

Note: the stepper motor just waiting consumes ~0.25A*12V = 3W!! And it gets hot!!  

--

After installing the Mega, the addresses `by-id` remain unchanged, but `by-path `addresses change:

| Mega4 USB port position (when plugged on top-right RPi USB port) | `/dev/serial/by-path/*` address |
| --- | --- |
| left: Addon Arduino microUSB, ej. LiDAR, gun | `/dev/serial/by-path/platform-fd500000.pcie-pci-0000:01:00.0-usb-0:1.2.3:1.0-port0` |
| center: gamepad dongle | `/dev/serial/by-path/platform-fd500000.pcie-pci-0000:01:00.0-usb-0:1.2.2:1.0-port0` |
| right: robot base Arduino | `/dev/serial/by-path/platform-fd500000.pcie-pci-0000:01:00.0-usb-0:1.2.1:1.0-port0` |
| side: Addon Arduino miniUSB ej.  clamp,  line follower | `/dev/serial/by-path/platform-fd500000.pcie-pci-0000:01:00.0-usb-0:1.2.4:1.0-port0` |

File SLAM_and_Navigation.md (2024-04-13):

# SLAM

## Intro

grid SLAM with a 2D LiDAR

mapping: requires global positioning to record environment

localization: using a map to determine position in global coordinate system

sometimes we only have starting point, detection and odometry and we need to do SLAM

2 categories: feature and grid SLAM. In grid we define a grid of cells and determine if they are occupied/unoccupied

navigation: using maps to determine safe trajectory between locations.

## Frame conventions

`base_link` is the frame attached to our robot

`odom` represents world origin as seen by odometry. Note odometry integrates wheel velocities, hence it is smooth but has small drift errors that accumulate over time.

`map` represents the true world origin,  and allows to visualize drift errors. `map` to `odom `jumps around but stays generally correct over time 

`base_footprint` frame is shadow of `base_link` on the 2D ground

## Install and Setup

1.  add `base _footprint` link to `robot_core.xacro`

```xml
<!-- BASE_FOOTPRINT LINK -->
    <joint name="base_footprint_joint type="fixed">
    <parent link="base_link"/>
    <child link="base_footprint"/>
    <origin xyz="0 0 0" rpy="0 0 0"/>
    </joint>
    
    <link name="base_footprint">
    </link>
```

2. install `slam_toolbox`

```bash
$ sudo apt install ros-foxy-slam-toolbox
```

We will run SLAM in online (live) asynchronous (may skip some scans but always process the latest) mode

Copy the parameter file to our project:

```bash
$ cp /opt/ros/foxy/share/slam_toolbox/config/mapper_params_online_async.yaml sevillabot/sevillabot/config/
```

Run with:

```bash
(PC T1)$ ros2 launch sevillabot launch_sim.launch.py world:=~/dev_ws/src/sevillabot/worlds/obstacles.world
```

Gazebo does not start!

First issue: Cannot import name 'GazeboRosPaths' error apparently caused by keeping python scripts in /scripts folder. I moved them to my_scripts.

After long troubleshooting and comparing with articubot_one from Josh Newans I found the differences:

* in file `rsp.launch.py`: add a new `sim_mode` parameter in the call made to `robot.urdf.xacro` , make it same value as `use_sim_time`
* in file `robot.urdf.xacro` declare `sim_mode` xacro parameter with `false` as default. Note this file uses `use_ros2_control` to toggle between `ros2_control.xacro` and a `gazebo_control.xacro`, which does not exist!!
* in `ros2_control.xacro` file use `sim_mode` to toggle between DiffDriveArduino (real robot) and GazeboSystem (simulation). Add `gaz_ros2_ctl_use_sim.yaml` parameter file in call to `libgazebo_ros2_control.so`
* Create `gaz_ros2_ctl_use_sim.yaml` parameter file that sets `use_sim_time` to  `true`

Launch also rviz:

```bash
(PC T2)$ rviz2 -d ~/dev_ws/src/sevillabot/config/bot_with_sensors.rviz
```

Launch teleop (would be better with gamepad if available):

```bash
(PC T3)$ ros2 run teleop_twist_keyboard teleop_twist_keyboard --ros-args -r /cmd_vel:=/diff_cont/cmd_vel_unstamped
```

Launch SLAM:

```bash
(PC T2)$ ros2 launch slam_toolbox online_async_launch.py params_file:=./src/sevillabot/config/mapper_params_online_async.yaml use_sim_time:=true
```

In RVIZ:

* add a Map and set the topic to /map

* change the Fixed Frame from odom to map (this to have the map steady)
* save RVIZ config to `slam_gazebo.rviz`

## Quick Start Guide SLAM on PC with keyboard

```bash
(PC T1)$ ros2 launch sevillabot launch_sim.launch.py world:=~/dev_ws/src/sevillabot/worlds/obstacles.world

(PC T2)$ ros2 launch slam_toolbox online_async_launch.py params_file:=./src/sevillabot/config/mapper_params_online_async.yaml use_sim_time:=true

(PC T3)$ rviz2 -d ~/dev_ws/src/sevillabot/config/slam_gazebo.rviz

(PC T4)$ ros2 run teleop_twist_keyboard teleop_twist_keyboard --ros-args -r /cmd_vel:=/diff_cont/cmd_vel_unstamped
```

Note: the above is now obsolete due to use of twist_mux

## Creating a map

Close everything an reopen

Make sure config file `mapper_params_online_async.yaml` is ok: set mode to mapping, map file and start commented out: 

```
mode: mapping # localization or mapping depending on the activity
...
# map_file_name: /home/mhered/sevillabot/sevillabot/maps/map_obstacles_serial
...
# map_start_at_dock: true
```

In RVIZ:

* Drive around to build the map
* May help to switch View to TopDownOrthographic

To save the map:

* In RVIZ Add New Panel
* save map for external services eg navigation produces PGM + YAML, serialize to reuse in slam_toolbox produces DATA + POSEGRAPH
* map files saved by default in the workspace `/dev_ws`

## Using a map

Close everything and reopen

Modify config file `mapper_params_online_async.yaml`: set mode to localization, declare map full path without extension and set start at dock 

```
mode: localization # localization or mapping depending on the activity
...
map_file_name: /home/mhered/sevillabot/sevillabot/maps/map_obstacles_serial
...
map_start_at_dock: true
```

## AMCL Adaptive MonteCarlo Localization

### Setup

Install Nav2 (acml is part of nav2)

```bash
$ sudo apt install ros-foxy-navigation2 ros-foxy-nav2-bringup
```

Several steps:

1. Run a map server (from save version because it is external):

```bash
(PC T1)$ ros2 run nav2_map_server map_server --ros-args -p yaml_filename:=/home/mhered/sevillabot/sevillabot/maps/map_obstacles_save.yaml -p use_sim_time:=true
```

2. Activate it

```bash
(PC T2)$ ros2 run nav2_util lifecycle_bringup map_server
```

3. Relaunch gazebo, RVIZ and slam_toolbox

In RVIZ take care Map is set to Reliable and Transient Local

4. run acml

```bash
$ ros2 run nav2_amcl amcl --ros-args -p use_sim_time:=true
```

5. activate it

```bash
$ ros2 run nav2_util lifecycle_bringup amcl
```

# Navigation

## Intro

Finding a safe trajectory between an initial and a target pose
We will need:

1. accurate position estimate ie localization from SLAM
2. awareness of obstacles from 1) a static prerrecorded map used for plnning the trajectory + 2) updated live sensor data. Stored in a costmap (avoid high cost, low cost is safe)
3. info about size and dynamics of the robot

## Install

```bash
$ sudo apt install ros-foxy-navigation2 ros-foxy-nav2-bringup
$ sudo apt install ros-foxy-twist-mux
```

## Multiplexing velocities

Will need to remap velocities from `/cmd_vel` where nav2 publishes to `/diff_cont/cmd_vel_unstamped` where our controller expects them, but instead we will use `twist_mux` node to multiplex velocities. This allows to prioritize, block topics on certain circumstances etc

We will set up `twist_mux` to take joystick velocities from `/cmd_vel_joy` and navigation velocities from `/cmd_vel` combine them and publish them to `/diff_cont/cmd_vel_unstamped` 

Modify   `joystick.launch.py` so it remaps velocities to  `/cmd_vel_joy` instead of directly to`/diff_cont/cmd_vel_unstamped` and add new file `twist_mux.yaml`:

```
twist_mux:
  ros__parameters:
    topics:
      navigation:
        topic: cmd_vel
        timeout: 0.5
        priority: 10
      joystick:
        topic: cmd_vel_joy
        timeout: 0.5
        priority: 100
```

1. Run with:

```bash
$ ros2 run twist_mux twist_mux --ros-args --params-file ~/dev_ws/src/sevillabot/config/twist_mux.yaml -r cmd_vel_out:=diff_cont/cmd_vel_unstamped

[INFO] [1712707933.767525498] [twist_mux]: Topic handler 'topics.joystick' subscribed to topic 'cmd_vel_joy': timeout = 0.500000s , priority = 100.
[INFO] [1712707933.767752264] [twist_mux]: Topic handler 'topics.navigation' subscribed to topic 'cmd_vel': timeout = 0.500000s , priority = 10.
```

2. Launch gazebo, RVIZ and slam_toolbox

3. Launch nav2

```bash
$ ros2 launch nav2_bringup navigation_launch.py use_sim_time:=true
```

4. In RVIZ add a new Map, set topic to `/global_costmap/costmap`, set Color Scheme to costmap, turn off the other map.
5. Set a 2D goal pose. It works!!

# Run SLAM & Navigation in the robot

## Install slam_toolbox and nav2 dependencies

```bash
$ sudo apt install ros-foxy-slam-toolbox
$ sudo apt install ros-foxy-navigation2 ros-foxy-nav2-bringup
$ sudo apt install ros-foxy-twist-mux
```

git pull to update the repo in the bot

## Setup Lidar LD06 on robot

1. Clone and symlink the repo:

```bash
(bot):$ cd ~/git
(bot):$ git clone https://github.com/ldrobotSensorTeam/ldlidar_stl_ros2
(bot):$ ln -s ~/git/ldlidar_stl_ros2/ ~/robot_ws/src/
```

2. Plug the LD06 and find out the device id (`by-id` because the path `/dev/ttyUSB*` may change):

```bash
(bot):$ ls /dev/serial/by-id
usb-1a86_USB2.0-Ser_-if00-port0
usb-Silicon_Labs_CP2102_USB_to_UART_Bridge_Controller_0001-if00-port0
```

Where `usb-Silicon_Labs_CP2102_USB_to_UART_Bridge_Controller_0001-if00-port0` is the LD06 ( and`usb-1a86_USB2.0-Ser_-if00-port0` is the arduino)

3. Set device permissions:

```bash
(bot):$ sudo chmod 777 /dev/serial/by-id/usb-Silicon_Labs_CP2102_USB_to_UART_Bridge_Controller_0001-if00-port0
```

4. Copy `ldlidar_stl_ros2/launch/ld06.launch.py` over to sevillabot repo, update`package_name` and  `port_name` then build the package and source:

```bash 
(bot):$ cp ~/robot_ws/src/ldlidar_stl_ros2/launch/ld06.launch.py ~/robot_ws/src/sevillabot/launch/ld06.launch.py
... # edit file
(bot):$ cd ~/robot_ws
(bot):$ colcon build 
(bot):$ source install/setup.bash
```

## Quick Start Guide robot with sensors

13/04/24 Updated `launch_robot.launch.py`and `launch_sim.launch.py` to spawn robot, launch gamepad and twist_mux with a single command

```bash
(robot T1):$ ros2 launch sevillabot launch_robot.launch.py #spawns robot, launches gamepad and twist_mux
```

Launch Lidar:

```bash
(robot T2):$ ros2 launch sevillabot ld06.launch.py
```

View it from PC with:	

```bash
(PC):$ rviz2 -d ~/dev_ws/src/sevillabot/config/bot_with_sensors.rviz
```

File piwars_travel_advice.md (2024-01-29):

# Traveling with the robot

We have started making travel arrangements and to ponder how we should transport our robot. Ship it in advance? Take it with us as checked-in or carry-on luggage? 

We searched for advice on the web and found some useful notes [here](https://www.reddit.com/r/FTC/comments/80q6u5/air_travel_with_ftc_robots/) and [here](https://fixit3491.com/fix-it-tips-and-tricks/traveling-ftc-robots/). Below a summary of our conclusions: 

1. Taking the robot as carry-on luggage mitigates some of the risk of damages. Taking it through security may be an adventure, though. Arrive to the airport early to give the luggage inspectors plenty of time to check your robot. 
2. Check the fine print: Airline fees for over size or over weight baggage can be usurious.  
3. Bring a letter explaining what is inside the box, and the competition in which you are going to take part. Be explicit: include pictures, list components, and highlight safety precautions taken for transport (e.g. batteries have been removed). Something like [this](https://www.firstchampionship.org/sites/default/files/first-tech-challenge/robot-airport-letter-houston-2017.pdf) or [this](https://fixit3491.com/wp-content/uploads/2018/02/robot-letter.pdf).
4. Airport inspectors will not appreciate a box of electronics connected to a battery. Therefore disconnect all batteries. Take them also in carry-on luggage but separately, in protective bags. As per EASA rules the maximum power allowed is 100 Wh, but that is a lot (the batteries of sevillabot are 55.5 Wh so well within that). Take with you the battery specs to facilitate the job of inspectors. See [EASA rules for transporting Lithium batteries](https://www.easa.europa.eu/en/domains/air-operations/dangerous-goods#lithium-batteries) and additional [practical information](https://www.easa.europa.eu/system/files/dfu/Background%20Information%20Lithium%20Batteries_update%20Sept%202017.pdf).
5. Make sure the robot is protected inside the box, either by packing a lot of foam and/or fastening the chassis of the robot to brackets attached to the box. You definitely don't want the robot resting on its axles, so make sure that the weight of the robot is on its chassis, not on the wheels. If using foam, take the wheels off or cut out the foam below them to avoid bending the axles. If using brackets, the robot itself should not touch the box, only the brackets.
6. You will need tools and spares, there is always a risk of damage during transport.  

We were relieved that the advice we found was encouraging us to take the robot as carry-on luggage, because the flights we were considering have less than 2 hours of connection to do a self-transfer between two legs, therefore too short for checked-in luggage anyway. 

Each airline seems to have slightly different constraints, so we need to take the most restrictive. In our case, we need an appropriate box under 55 x 40 x 20 cm in size, and with a total weight (including contents) under 10 kg. We also need shock protection, foam padding and wheels to move around the airport. 

* The gold standard seems to be Pelican 1510: shock resistant, padded with pre-diced foam, wheels and handle, IP67, weighs 6 kg empty!, and costs over 300€. See it at [pelican.com](https://www.pelican.com/us/en/product/cases/carry-on-case/protector/1510?sku=1510-000-190) or [amazon.es](https://www.amazon.es/PELI-resistente-telesc%C3%B3pica-impermeable-personalizable/dp/B000XYMZ4M/). 
* This [Amazon basics](https://www.amazon.es/dp/B01L0LVLLY/) seems quite ok for 134€, but weighs 7 kg! (and looking at the pictures we have doubts if the foam is actually pre-diced)
* This [HMF ODK400](https://www.amazon.es/gp/product/B08K3Q44MV/) costs 86€ but still weighs 7 kg
* This [MAX505S](https://www.amazon.es/Plastica-Panaro-MAX505S-Maleta-Alveolar/dp/B00PUL5TAK/) costs 127€, and weighs 4 kg, but has no wheels.
* An inexpensive - and lighter - alternative may be to mod a basic trolley (e.g. [this one](https://www.amazon.es/gp/product/B0CD2X69VD/) costs 66€ and weighs 2.8 kg) with a kit of pre-diced foam, which costs around 30€, and weighs under 600 g see e.g. [this one in amazon.es](https://www.amazon.es/dp/B08NG2BBJ4/). Under 100€ and 3.4 kg. 

Finally, we may need to send tools in advance as I doubt they will be alloed as carry-on...

# Outbound Flight

## 18/4 SVQ - PMI Vueling 3941 8:50 - 10:25

Booking code QIRNWG (551,35€)

Duration 1 h 35'

Seats booked in row 27. 

We all have 2 pieces of carry-on luggage: 

- 1 piece 40 x 20 x 30 cm, under the seat
- 1 piece 55 x 40 x 20 cm, max 10 kg, in overhead compartment

### There is 1 h 45' for the self-transfer in Palma de Mallorca. 

## 18/4 PMI- LTN Wizz Air W95352 12:10 - 13:50 

Confirmation code IL7UHN (412,23€)

Duration 2 h 40'

Seats booked in row 8. 

Everyone except Jose have Priority (1 piece 40 x 20 x 30 cm under the seat + 1 piece 55 x 40 x 23 cm, max 10 kg in overhead compartment). Jose only has the smaller piece under the seat. This could cause problems in the priority boarding.

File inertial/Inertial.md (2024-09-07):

## Inertial properties

Tutorials recommend [Solidworks Exporter](http://wiki.ros.org/sw_urdf_exporter) to calculate inertial properties (mass, centre of mass, inertia tensor) from CAD models . However I have designed in FreeCAD. 

I found sources for several methods to obtain inertial properties from FreeCAD models:

* Method 1 - directly in FreeCAD: see [JOKO Engineeringhelp - video tutorial on obtaining mass properties in FreeCAD](https://www.youtube.com/watch?v=gThQk-4p1CY)

* Method 2: This [Gazebo answers Q&A](https://answers.gazebosim.org//question/28772/meshlab-calculate-moments-of-inertia-not-assuming-density-of-1/) links to this excellent [tutorial on Inertial parameters of triangle meshes](https://classic.gazebosim.org/tutorials?tut=inertia&cat=build_robot) which recommends using [Meshlab](https://www.meshlab.net/) and also has a great discussion

* Method 3: this [tutorial](https://www.youtube.com/watch?v=CPViCzK7CUo&t=1809s) to approximate inertia for any 3D object using voxels

* Not explored yet: [Release of RobotCAD (FreeCAD OVERCROSS) v2.0.0](https://discourse.ros.org/t/released-v2-0-0-robotcad-freecad-overcross/38969) - workbench to generate robot description packages (xacro or URDF) for ROS2 - [official Github repo](https://github.com/drfenixion/freecad.overcross)

* Not explored yet: [Discussion on Tools and Best Practices for 3D Robot Assets (URDF, SDFormat, CAD, etc)](https://discourse.ros.org/t/discuss-tools-and-best-practices-for-3d-robot-assets-urdf-sdformat-cad-etc/36997)

## `<inertial>` tag

Example `<inertial>` tag:

```xml
<inertial>
    <origin xyz="-0.00000e+00 -0.00000e+00 3.00000e-02" rpy="0 0 0" />
    <mass value="2.00000e-01"/>
    <inertia ixx="7.0577869e-05" ixy="1.3099873e-13" ixz="-4.4938763e-14" iyy="7.0577869e-05" iyz="0.0000000e+00" izz="2.1155751e-05"/>
</inertial>
```

The `<mass>` should be entered in kilograms and you have to find it out experimentally (or from specifications, e.g. density x calculated volume): **measured mass (kg)**

The `<origin>` is used to enter the Center of Mass position (relative to the link's  origin; especially not relative to the link's visual or collision origin): **Center of mass coordinates (m).**

If you estimated the center of mass experimentally, fill in this value, otherwise fill in the correctly scaled value computed from the model. *The rotational elements can define a different coordinate for the moment of inertia axes.* (Meaning??)

The `<inertia>` tag contains the inertia tensor. Since the matrix is symmetric, only 6 numbers are sufficient to represent it:

```
| ixx ixy ixz |
| ixy iyy iyz |
| ixz iyz izz |
```

Quick check of tensor: 

* diagonal entries should have the largest values and be positive, and the off-diagonal numbers should more or less approach zero.
* The matrix has to be positive definite (use your favorite maths tool to verify that). 
* Its diagonal entries also have to [satisfy the triangle inequality](http://physics.stackexchange.com/a/48273), ie. `ixx + iyy >= izz`, `ixx + izz >= iyy` and `iyy + izz >= ixx`.

## Example 1 - bushing

As example we create a hollow cylinder (bushing) with the following properties:

- height: 60mm
- Outer diameter: 25mm 
- Inner diameter: 15mm 
- mass: 200g

Original FreeCAD model [bushing.FCStd](./assets/bushing.FCStd) | Exported STL [bushing.stl](./assets/bushing.stl)

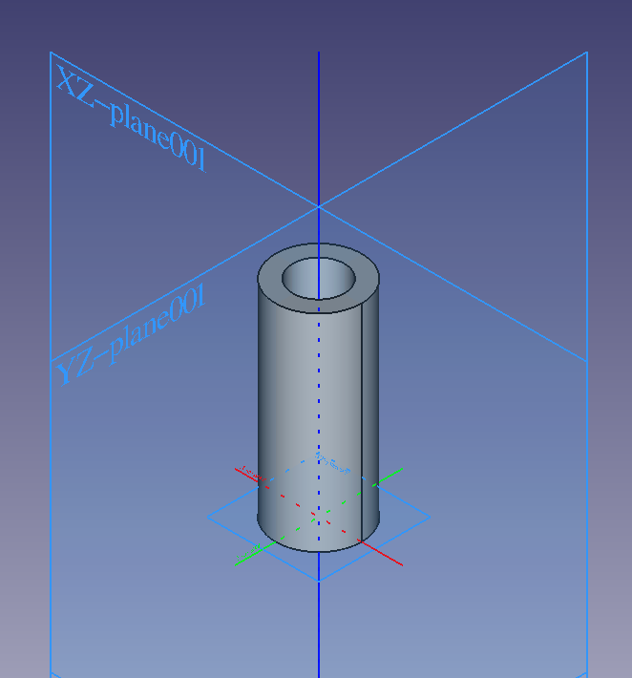
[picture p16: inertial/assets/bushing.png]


### Theoretical inertia tensor

The inertia tensor according to ChatGPT:

```
[[7.0625e-05 0.0000e+00 0.0000e+00]
[0.0000e+00 7.0625e-05 0.0000e+00]
[0.0000e+00 0.0000e+00 2.1250e-05]]
```

Can be checked manually with the formulas in [Wikipedia](https://en.wikipedia.org/wiki/List_of_moments_of_inertia#List_of_3D_inertia_tensors), or running `bushing_sample.py`, a python script that implements the formulas. It yields the same result, so we take this as a reference. 

### Method 1 - FCInfo macro in FreeCAD

cfr. [JOKO Engineeringhelp - video tutorial on obtaining mass properties in FreeCAD](https://www.youtube.com/watch?v=gThQk-4p1CY)

1. In FreeCAD install the Addon macro **FCInfo**

2. Open the FreeCAD model and select the **Body**

3. **Macro -> Macros... -> User macros -> FCInfo.FCMacro -> Execute**

This macro opens s side panel that allows clicking to get point coordinates, perimeters and surfaces of selected faces, as well as volume, mass and inertia tensor of bodies.

4. Enter density (or adjust manually to reach measured mass), in our case, to get 200g mass: density = 10.61kg/dm³ 
5. Scroll down and create a **Spreadsheet** with the data
6. Export it as CSV: **Spreadsheet Workbench -> Menu Spreadsheet -> Export spreadsheet**:  `bushing_freecad_data.csv`

```
...
'Matrix inertia massique	'gmm2				
' X:	70622.8065	' Y:	0	' Z:	-0
' X:	0	' Y:	70622.8065	' Z:	0
' X:	-0	' Y:	0	' Z:	21249.34
...
```

6. Remember you need to convert units. In our case:  g mm2 = 10⁻⁹ Kg m2. Manually:

```
Matrix inertia(kgm2)				
[[7.06228065e-5	0	-0]
[0	7.06228065e-5	0]
[-0	0	2.124934e-5]]
```

It checks!

Pending:

- [ ] write a python script to read from this CSV file the center of mass coordinates, volume, moment of inertia etc and generate the <inertial> tag. Note: careful, the CSV generated by FreeCAD keeps all the saves one after another, the script should take the most recent!!

### Method 2: Meshlab

Install meshlab from AppImage (version 2023):

1. Open a STL or DAE model

2. **Filters > Quality Measure and Computations > Compute Geometric Measures** to compute inertial values

3.  manually copy the output to a text file `bushing_meshlab_data.txt` :

```
...
Mesh Bounding Box Size 25.000000 24.930096 60.000000
...
Mesh Volume is 18807.816406
Center of Mass is -0.000000 -0.000000 30.000002
Inertia Tensor is :
| 6637078.000000 0.012319 -0.004226 |
| 0.012319 6637078.000000 0.000000 |
| -0.004226 0.000000 1989467.375000 |
...
```

Note: inertia tensor is in mm⁻⁵ , needs to be converted to m⁻⁵ then multiplied by the density in Kg/m³ :  

* 1 mm⁻⁵ = 1e-15 m⁻⁵

* Density = .2 Kg / 1.8807816406e-5 m³ =1.0633877e4 Kg/m3 

So the factor is 1.0633877e-11. Manually:

```Matrix inertia(kgm2)				
[[7.057787*e-5	~1e-11	~1e-11]
[~1e-11	7.057787*e-5	~1e-11]
[~1e-11	~1e-11	2.115575*e-5]]
```

The python script `inertial.py`  automates writing the <inertial> tag from the Meshlab log.

weight_factor = **measured mass (kg)** / `Mesh Volume`

length_factor = **measured bounding box (m)** / `Mesh Bounding Box Size`

**Center of mass coordinates (m)** = Center of Mass * length_factor

**i<sub>xy</sub> (kg*m<sup>2</sup>)** = weight_factor * length_factor<sup>2</sup>* `i_xy`* **s**<sup>-5</sup>

Output of running `inertial.py` script on `bushing_meshlab_data.txt` (the output of Meshlab on `bushing.stl`) is quite correct:

```xml
<inertial>
	<origin xyz="-0.00000e+00 -0.00000e+00 -0.00000e+00" rpy="0 0 0" />
	<mass value="2.00000e-01"/>
	<inertia ixx="7.0577880e-05" ixy="1.3099873e-13" ixz="0.0000000e+00" iyy="7.0577880e-05" iyz="-0.0000000e+00" izz="2.1155751e-05"/>
</inertial>
```

Tips and tricks in Meshlab:

Try **Filters > Cleaning and Repairing > Remove Duplicate Faces** to remove duplicate faces if needed

If values are too low and precision is lost: **Filters > Normals, Curvatures and Orientation > Transform: Scale** scale by **s**=10 or 100 (then later need to correct inertial values by 1/**s**⁵)

### Method 3 - Voxel approximation

cfr: https://www.youtube.com/watch?v=CPViCzK7CUo&t=1809s

Voxelize the STL using e.g. [voxelizer](https://drububu.com/miscellaneous/voxelizer/index.html?out=txt)

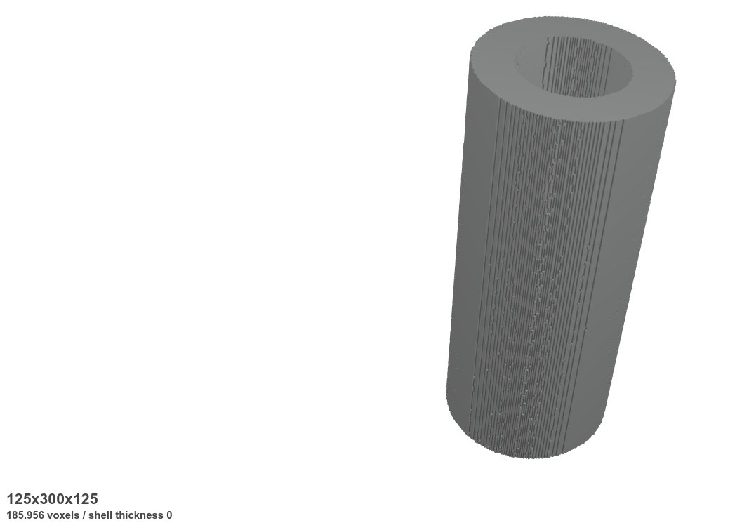
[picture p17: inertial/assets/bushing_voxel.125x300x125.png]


```bash
$ python3 voxel_inertia.py 
{'max_dimensions': [124.0, 124.0, 299.0], 'volume': 185956, 'center_of_mass': [0, 0, 0], 'inertia_tensor': {'i_xx': 10182.42249522264, 'i_yy': 10183.705798799883, 'i_zz': 2935.151186301868, 'i_xy': 1.2039471023613897e-10, 'i_xz': 1.5628747777305165, 'i_yz': -1.3182799040042368}}
Enter the measured mass in kg: .2
Mesh max_dimensions vector: [124.0, 124.0, 299.0]
Enter the dimension to scale (x, y, z)?: z
Enter a measured dimension in meters for scale: .6
<inertial>
    <origin xyz="0.00000e+00 0.00000e+00 0.00000e+00" rpy="0 0 0" />
    <mass value="2.00000e-01"/>
    <inertia ixx="4.4099233e-08" ixy="5.2141957e-22" ixz="6.7686819e-12" iyy="4.4104791e-08" iyz="-5.7093617e-12" izz="1.2711898e-08"/>
</inertial>
```

## Example 2: a box

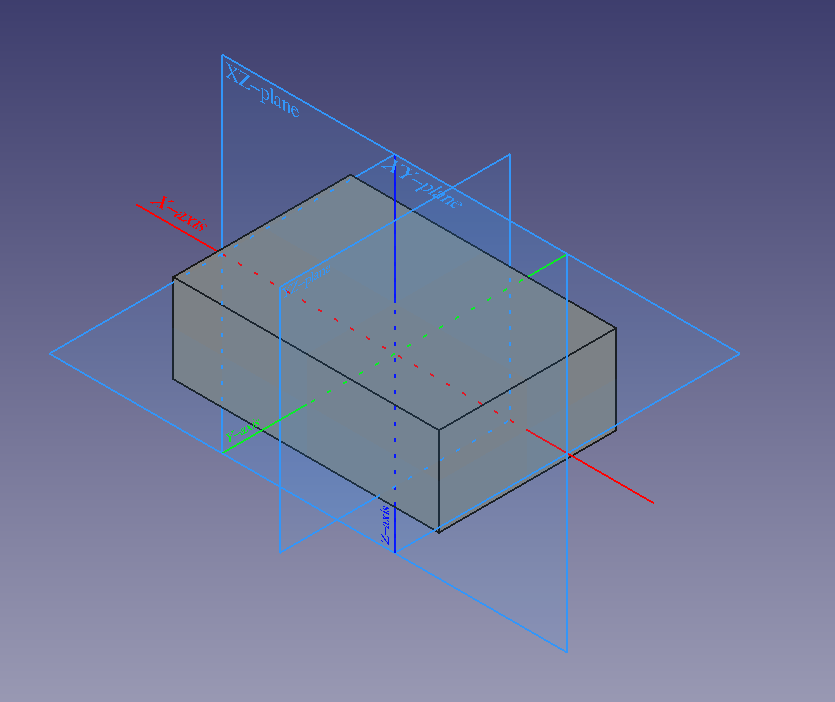
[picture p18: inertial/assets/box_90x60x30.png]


A simple box:

* x: 90mm
* y: 60mm
* z: 30mm

* mass: 1.5kg

Original FreeCAD model [box_90x60x30.FCStd](./assets/box_90x60x30.FCStd) | Exported STL [box_90x60x30.stl](./assets/box_90x60x30.stl)

### Theoretical inertia tensor

```python
[[5.625e-4, 0.0, 0.0],
    [0.0, 1.125e-3, 0.0],
    [0.0, 0, 1.4625e-3]]
```

### Method 1 - FCInfo macro in FreeCAD

Adjust density = 9.2593 kg/dm³ to get mass ~1.5 kg 

Export Spreadsheet to `box_90x60x30_freecad_data.csv`

```
'Matrix inertia massique	'gmm2				
' X:	562502.475	' Y:	0	' Z:	0
' X:	0	' Y:	1125004.95	' Z:	0
' X:	0	' Y:	0	' Z:	1462506.435
```

Convert units: 1 g mm² = 10⁻⁹ Kg m²

```python
[[5.62502475e-4,	0,	0]
[0,	1.12500495e-3,	0]
[0,	0,	1.462506435e-3]]
```

### Method 2: Meshlab

Opened `box_90x60x30.stl` in Meshlab and analyzed. Manually copied the log output to a text file `box_90x60x30_meshlab_data.txt` :

```
...
Mesh Bounding Box min -45.000000 -30.000000 -15.000000
Mesh Bounding Box max 45.000000 30.000000 15.000000
Mesh Volume is 162000.000000
Center of Mass is 0.000000 0.000000 0.000000
Inertia Tensor is :
| 60750000.000000 0.000000 0.000000 |
| 0.000000 121500000.000000 0.000000 |
| 0.000000 0.000000 157950000.000000 |
...
```

Note: inertia tensor is in mm⁵ , needs to be converted to m⁵ then multiplied by the density in Kg/m³ :  

* 1 mm⁵ = 1e-15 m⁵

* Density = 1.5 Kg / 1.62e-4 m³ =9.25926e+3 Kg/m3 

So the factor is 9,25926e-12. Manually:

```Matrix inertia(kgm2)				
[[5.6250e-4	0	0]
[0	1.125e-3	0]
[0	0	1.46250012e-3]]
```

### Method 3 - Voxel approximation

Voxelize the STL using e.g. [voxelizer](https://drububu.com/miscellaneous/voxelizer/index.html?out=txt) 

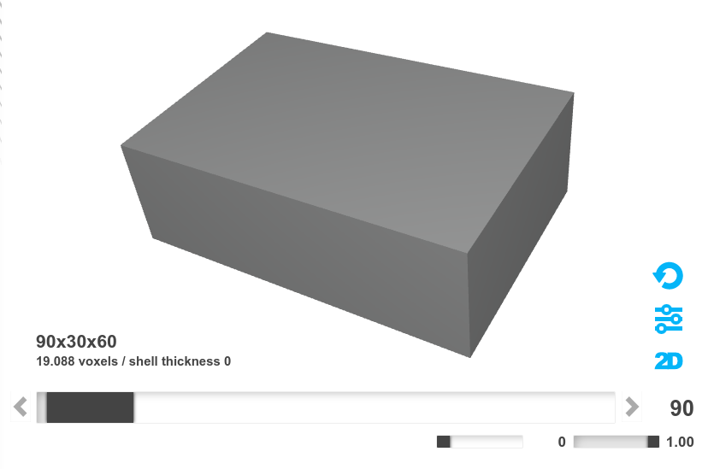
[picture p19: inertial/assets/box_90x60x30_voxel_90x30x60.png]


Actually created 3 versions:

Output with [box_90x60x30_voxel_9x3x6.txt](./inertia/test_samples/box_90x60x30_voxel_9x3x6.txt) 

```
<inertia ixx="7.3276119e-04" ixy="-0.0000000e+00" ixz="-0.0000000e+00" iyy="1.4453731e-03" iyz="-0.0000000e+00" izz="1.8879851e-03"/>
```

With [box_90x60x30_voxel_90x30x60.txt](./inertia/test_samples/box_90x60x30_voxel_90x30x60.txt):

``` 
<inertia ixx="5.0892461e-04" ixy="-0.0000000e+00" ixz="-0.0000000e+00" iyy="8.9406903e-04" iyz="-0.0000000e+00" izz="1.1507949e-03"/>
```

With [box_90x60x30_voxel_900x300x600.txt](./inertia/test_samples/box_90x60x30_voxel_900x300x600.txt):

```
 <inertia ixx="5.1003402e-04" ixy="-8.7047660e-07" ixz="-7.5568927e-06" iyy="8.1515719e-04" iyz="3.8551550e-07" izz="1.0656610e-03"/>
```

Does not seem to converge...

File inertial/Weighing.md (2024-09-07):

# CoG from weighing

A: contact point of castor

B: contact point of left wheel

C: contact point of right wheel

Coordinate frame: 

XY plane on lower face of Aluminum frame

X middle point between wheels pointing forward

Z pointing upwards

Y pointing left to follow right hand convention

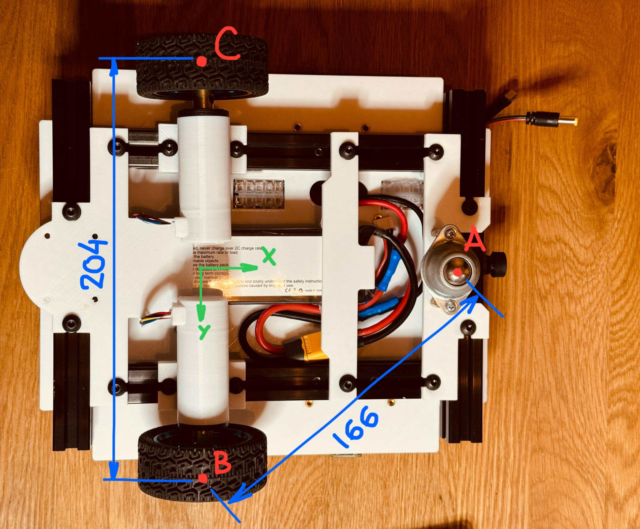
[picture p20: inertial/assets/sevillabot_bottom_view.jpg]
 

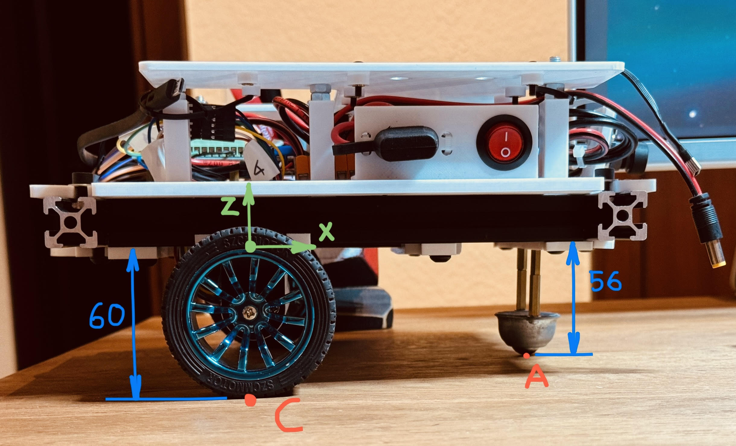
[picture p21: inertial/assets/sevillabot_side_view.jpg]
 

| Measured dimensions | x (mm) | y (mm) | z (mm) |
| --- | --- | --- | --- |
| A | 131 | 0 | -56 |
| B | 0 | 102 | -60 |
| C | 0 | -102 | -60 |

To calculate x coordinate of A:

l' ² + 102² = 166² -> l' ~= 131 mm

l²+4² = l'² -> l ~= 131 mm (no effect of the 4mm )

| Raised: 9.3mm | W_A (g) | W_B (g) | W_C (g) | Sum (g) |
| --- | --- | --- | --- | --- |
| None | 545.7 | 708.8 | 641.3 | 1895.8  |
| A | 511.8 | 719.2 | 665.0 | 1896 |
| B | 586.5 | 684.0 | 624.8 | 1895.3  |
| C | 589.2 | 696.5 | 609.8 | 1895.5  |

W = 1895.7 g

Subtract weight of wheels: 45.4 g each on points B and C

Subtract weight of castor: 47.1g on point A

Result: 1757.8g

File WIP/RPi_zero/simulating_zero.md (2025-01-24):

# Developing for RPi without an RPi

[install Fritzing](https://fritzing.org/download/)

downloaded custom SSD1306 Fritzing part from [here](https://forum.fritzing.org/t/oled-128x64-i2c-monochrome-display-ssd1306-created/1202)

[install Wyliodrinstudio](https://wyliodrin.studio/): 2.3.2 AppImager

followed this tutorial: https://www.youtube.com/watch?v=rTg7YT11pKA

export SVG and XML list from Fritzing into Wyliostudio

library to control SSD1306 in python from RPi: https://github.com/rm-hull/luma.examples

[Enable SPI and I2C on Ubuntu 20.04 Raspberry Pi](https://askubuntu.com/questions/1273700/enable-spi-and-i2c-on-ubuntu-20-04-raspberry-pi)

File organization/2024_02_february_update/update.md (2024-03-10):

Hello Piwars organization.

A bit over two months to go and the Sevillabot team continues in good spirits, making steady progress. We remain generally on schedule, although admittedly we decided to go for remote control wherever possible and focused our efforts on some of the challenges which seemed more accessible or fun.

- robot base: all parts printed and assembled, all components installed, wired, and software set up. First power on with batteries achieved, and the robot responds correctly to basic commands. To do: troubleshoot control with gamepad (started misbehaving after migration to humble), then practice practice practice handling which will probable lead to some iterations of improvements

- eco disaster add-on: we made a beautiful clamp extension to grab barrels, including 3D printed parts, components and software. The clamp is fully assembled and working well in initial tests separated from the robot. To do: connect the extension to the robot base and practice a lot.  

- zombie apocalypse add-on: almost complete, and we are quite proud of this one as it includes laser targeting, and the 3D printed mechanisms needed for aiming up and down and firing a Nerf gun. Horizontal aiming is achieved turning the robot. Already tested (separately from the robot) and we confirm killing zombies is fun! To do: fix a bug that is causing "bouncing" in the trigger, design the mechanical attachment to the upper deck of the robot base itself and some minor improvements in the layout and wiring of components. 

- lava palava add-on: line sensor support parts designed in FreeCAD and printing ongoing. Basic bang-bang line follower algorithm implemented. To do: assemble add-on, then test and fine-tune the algorithm on the real robot.

- escape route: we added a camera to the robot base and camera streaming from the robot is already working. To do: build a mockup maze then practice practice practice. If necessary we may add a Lidar (already available and tested). 

- minesweeper challenge: we plan to do it remote controlled, without add-ons. To do: practice handling!

- temple of doom: To do: practice handling across obstacles

- pi noon: To do: install the terminal block and practice sparring (finished sevillabot vs initial prototype)

- logistics: flights & hotels already booked. Working on uniformed T-shirts for the team and a solution to bring with us on the flight the bot and the tools (any advice welcome)

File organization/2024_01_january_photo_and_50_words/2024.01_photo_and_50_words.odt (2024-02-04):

"We are a family of aspiring roboticists from sunny Sevilla in Spain: mum, dad and 3 boys aged 6, 9 and 12. We have built a differential-drive robot with different accessories such as a gripper for Eco-Disaster, a Nerf turret for Zombie Apocalypse or a line sensor for Lava Palava".

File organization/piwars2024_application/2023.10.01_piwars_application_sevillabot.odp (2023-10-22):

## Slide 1

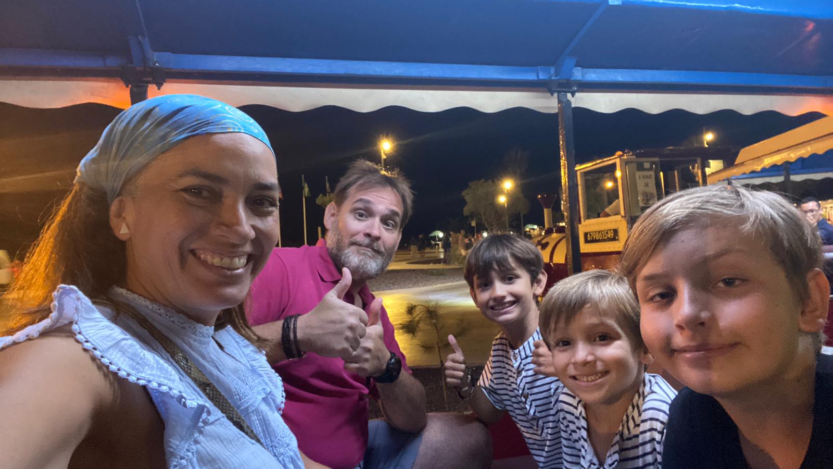
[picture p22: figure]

sevillabot

Meet the team!

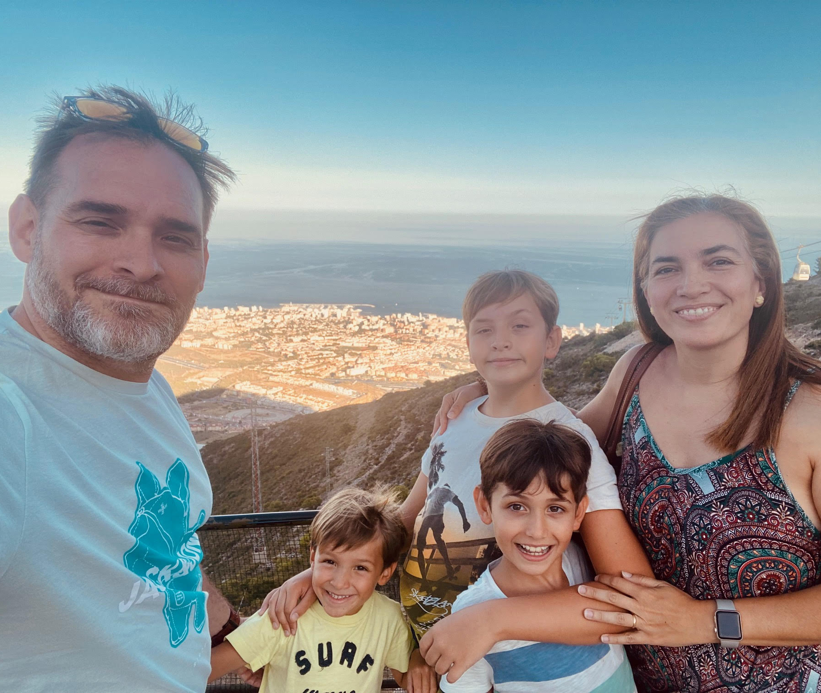
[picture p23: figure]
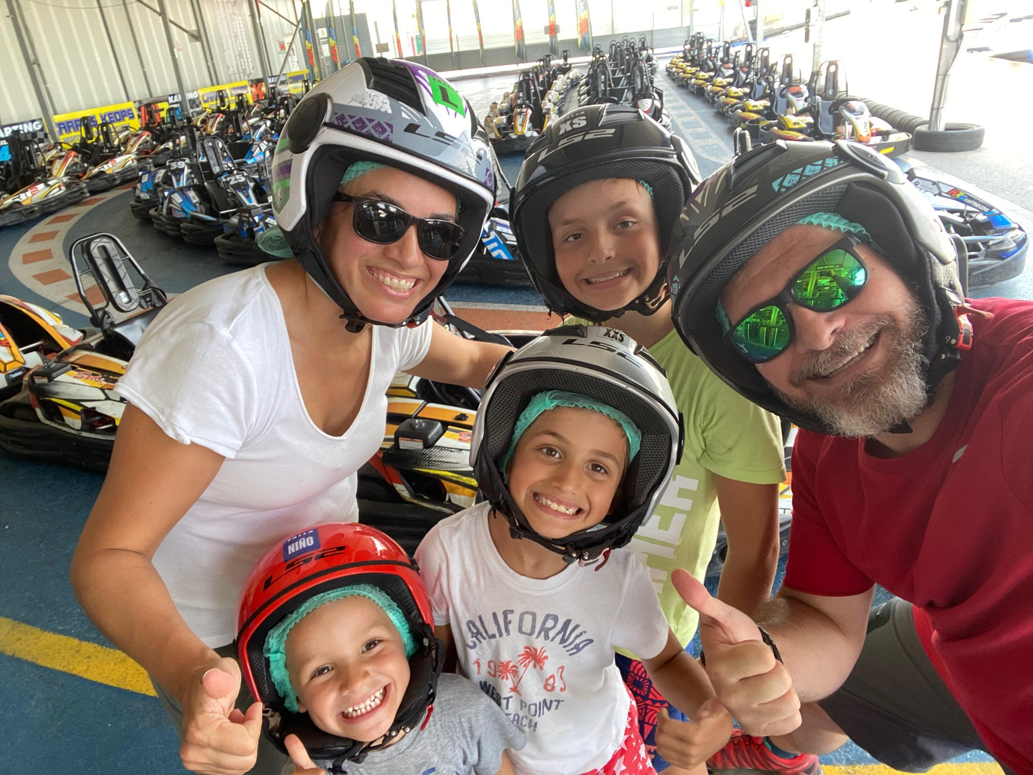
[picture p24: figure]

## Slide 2


sevillabot

Meet the bot!


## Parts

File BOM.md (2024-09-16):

# Bill of Materials

Total approx price **498,47€** (+ cost of standards and consumables)

| Qty  | Item | Image | Description | Link | Pack Price (€) | Pack Size | Unit Price (€) | Subtotal (€) |
| ---- | --- | --- | --- | --- | --- | --- | --- | --- |
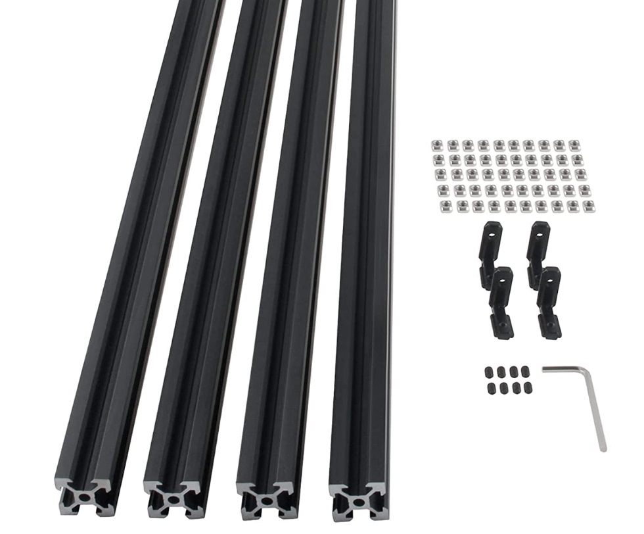
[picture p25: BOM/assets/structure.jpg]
| 1 | [Structure](./BOM/Structure.md) |  | CNCMANS 4 x 200mm EU2020-T anodized aluminium profiles | [Amazon](https://www.amazon.es/dp/B0BX686QY5) | 17.00 | 1 | 17.00 | 17.00 |
| many | [3D printed parts](./BOM/3D_printed_parts.md) | | | | | | | 0.00 |
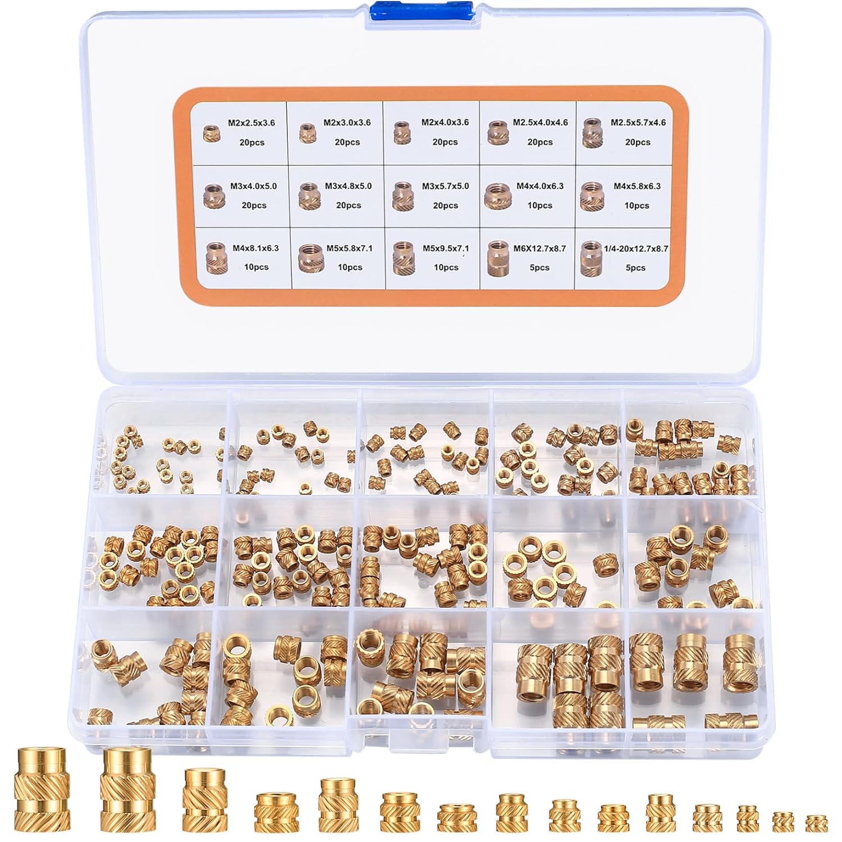
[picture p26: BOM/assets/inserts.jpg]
| many | [Inserts](./BOM/inserts.md) |  | Heat set inserts | [Amazon](https://www.amazon.es/gp/product/B0B2DMWFT2/) | 10.99 | 220 | 0.05 | 10.99 |
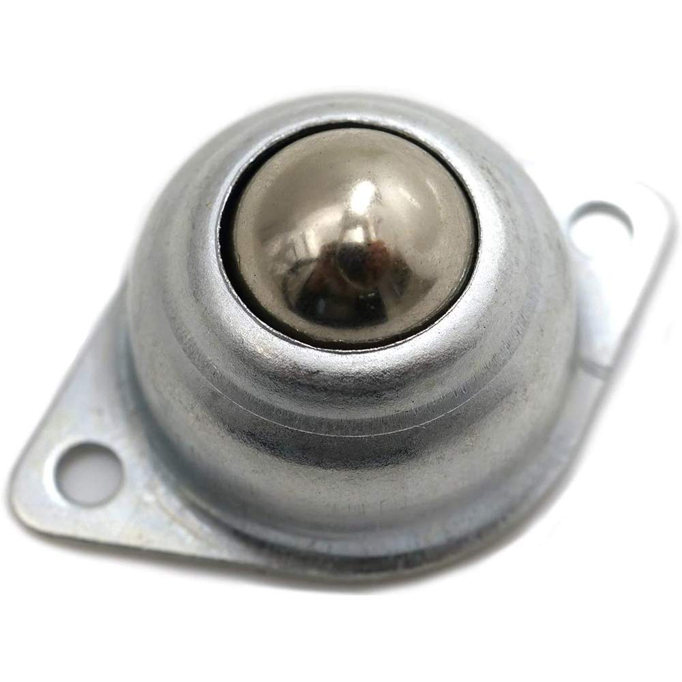
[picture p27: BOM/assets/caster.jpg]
| 1 | [Caster wheel](./BOM/caster.md) |  | | [Amazon](https://www.amazon.es/dp/B09MLVQWL7) | 12.59 | 6 | 1.49 | 1.49 |
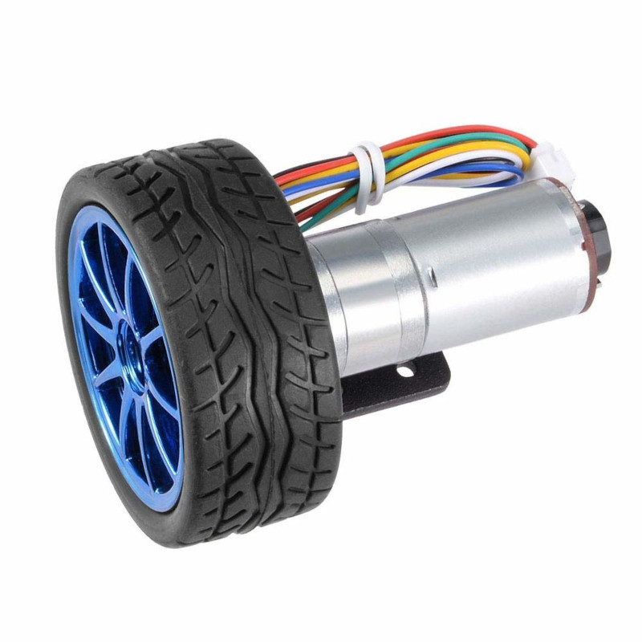
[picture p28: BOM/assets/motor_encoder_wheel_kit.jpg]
| 2 | Motor and wheel kit |  | 12V motor encoder and wheel kit (130rpm) | [Amazon](https://www.amazon.es/dp/B07WT22RNK) | 23.92 | 1 | 23.92 | 47.84 |
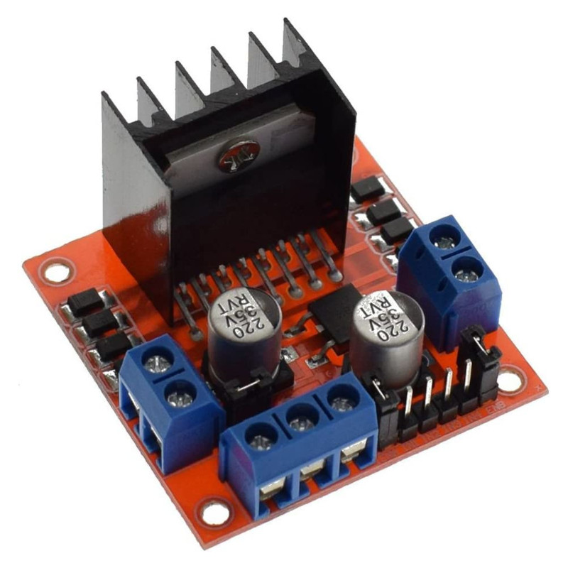
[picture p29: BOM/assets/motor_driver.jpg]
| 1 | [L298N Motor driver](./BOM/motor_driver.md) |  | | [Amazon](https://www.amazon.es/gp/product/B077NY9RY6/ref=ppx_yo_dt_b_asin_title_o00_s01?ie=UTF8&psc=1) | 9.99 | 2 | 4.99 | 4.99 |
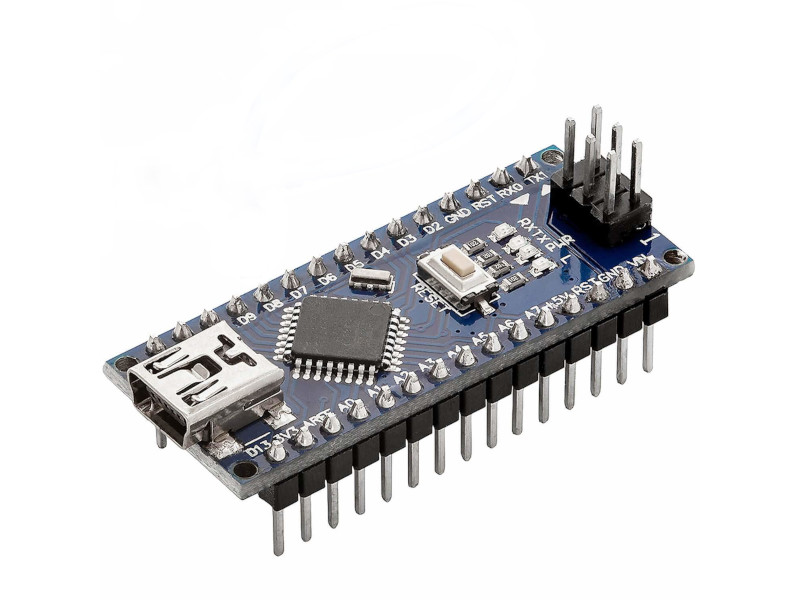
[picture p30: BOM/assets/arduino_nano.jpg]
| 4 | Arduino Nano |  | AZDelivery AZ-Nano V3-Board w/ Atmega328 CH340 | [Amazon]() | 21.99 | 3 | 7.33 | 29.32 |
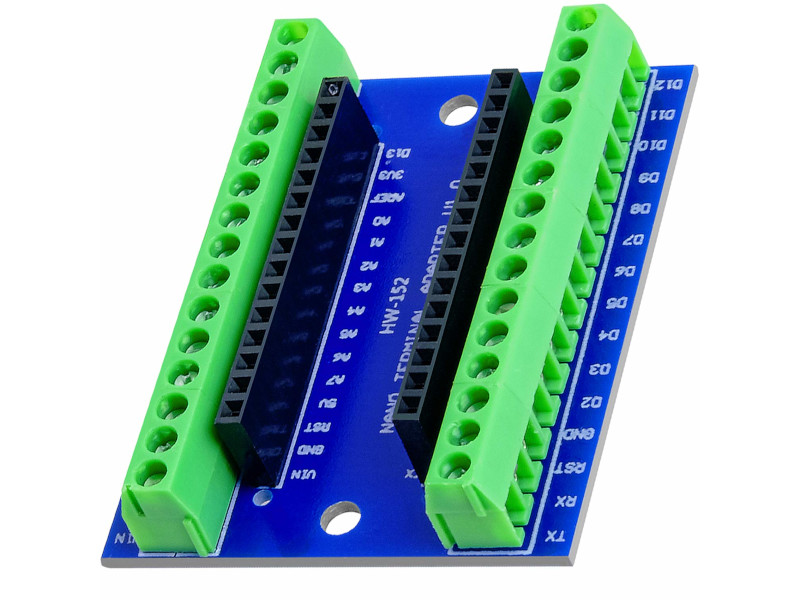
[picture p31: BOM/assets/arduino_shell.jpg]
arduino_shell
| 1 | Arduino Nano Shell |  | | [Amazon](https://www.amazon.es/gp/product/B08T1ZXS7K/ref=ppx_yo_dt_b_asin_title_o00_s01?ie=UTF8&th=1) | 6.99 | 1 | 6.99 | 6.99 |
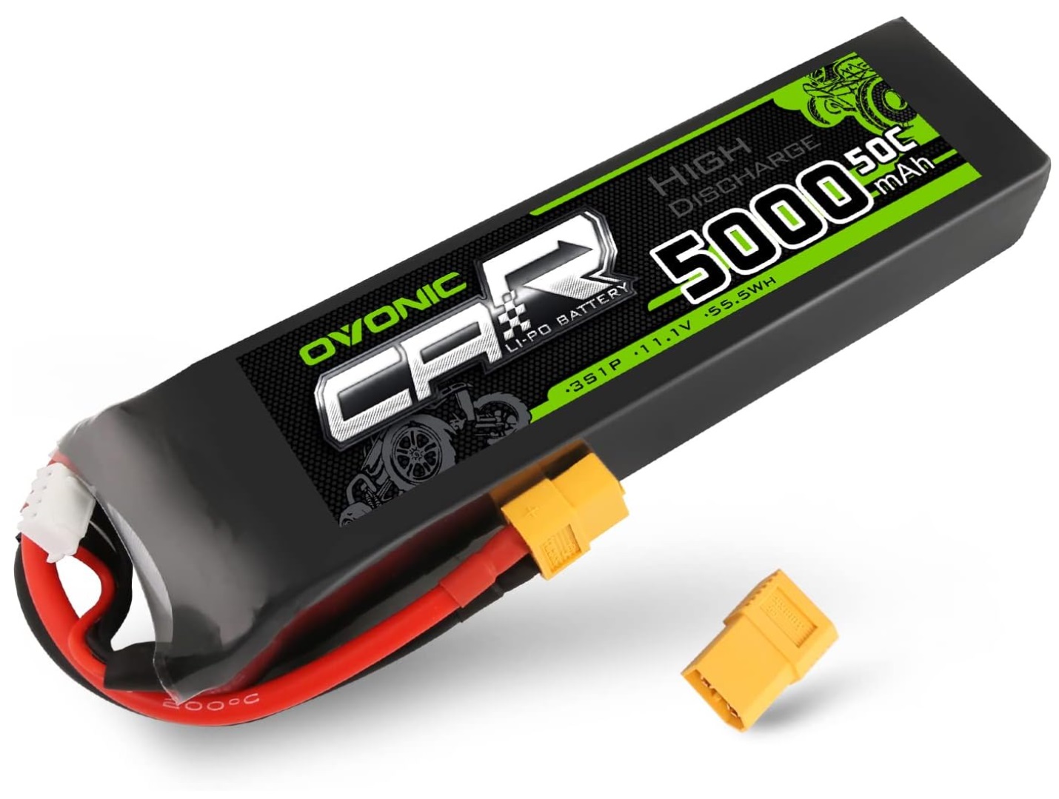
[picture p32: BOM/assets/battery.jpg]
| 1 | Battery |  | OVONIC LiPo 3S 5000mAh 50C 11.1V with XT connector | [Amazon]() | 39.99 | 1 | 39.99 | 39.99 |
| 1 | [DC-DC Buck converter](./BOM/buck_converter.md) |  | ICQUANZX DC-DC 5A 5-32V input to 0.8-24V output | [Amazon](https://www.amazon.es/dp/B07VQ89RZG) | 21.99 | 3 | 7.33 | 7.33 |
| 1 | [Raspberry Pi 4B](./BOM/RPi_4B.md) | raspberry-pi-4-modelo-b-4gb | Raspberry Pi 4B 4Gb | [Electronica Embajadores](https://www.electronicaembajadores.com/es/Productos/Detalle/LCRBPI4B4/modulos-electronicos/raspberry-pi/raspberry-pi-4-4gb-tarjeta-ordenador-sc0194-9/) | 99.03 | 0 | 99.03 | 99.03 |
| 1 | [Mega4 USB Hub](./BOM/mega4.md) | mega4 | UUGEAR MEGA4: 4-Port USB 3.1 PPPS Hub for Raspberry Pi 4B | [The Pi Hut](https://thepihut.com/products/mega4-4-port-usb-3-1-ppps-hub-for-raspberry-pi-4) | £29.00 | 1 | £29.00 | £29.00 |
| 1 | USB flat cable 100mm |  | Straight USB (AMST) to straight Mini USB (V3ST) | [Aliexpress](https://es.aliexpress.com/item/1005002551406991.html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) | 6.91 | 2 | 3.46 | 3.46 |
| 1 | Gamepad |  | Logitech F710 Gamepad | [Amazon](https://www.amazon.es/dp/B00CJAEX5M) | 44.81 | 1 | 44.81 | 44.81 |
| 1 | Nerf |  | Nerf Modulus Stryfe | [Amazon](https://www.amazon.es/gp/product/B072PYD365) | 42.07 | 1 | 42.07 | 42.07 |
| 2 | [28BYJ-48_Stepper motor](./BOM/28BYJ-48_stepper.md) |  | 28BYJ-48 12V stepper motor with ULN2003A based driver board | [Amazon](https://www.amazon.es/Reland-Sun-28BYJ-48-ULN2003-controlador/dp/B09QQLMYWP/) | 3,57 | 1 | 7.14 | 7.14 |
| 1 | [Linear Actuator](./BOM/Linear actuator.md) |  | ETOPAR 12V linear actuator for car door locking | [Amazon](https://www.amazon.es/gp/product/B08NG6LTY2) | 16.79 | 4 | 4.20 | 4.20 |
| 1 | Relay |  | 1 channel 5V relay | [Amazon](https://www.amazon.es/gp/product/B09GY34ZFQ) | 11.69 | 6 | 1.95 | 1.95 |
| 1 | [Laser pointer](./BOM/laser_pointer.md) |  | GALDOEP 650nm 5mW red laser diode module 3-5V | [Amazon](https://www.amazon.es/dp/B09J3TB26H) | 9.99 | 3 | 3.33 | 3.33 |
| 2 | Micro switches |  | WANGCL micro switches | [Amazon](https://www.amazon.es/gp/product/B0B1MMQ3RT/) | 6.99 | 50 | 0.14 | 0.28 |
| 1 | [Line sensor](./BOM/line_sensor.md) |  | Pololu QTR-8RC reflectance sensor array | [Electronica Embajadores](https://www.electronicaembajadores.com/es/Productos/Detalle/SSIRQTR/sensores/sensores-de-infrarrojos/qtr-8rc-array-sensores-de-reflexion/) | 15.12 | 1 | 15.12 | 15.12 |
| 1 | [DTOF Lidar LD06](./BOM/LD06-lidar.md) | LD06-lidar | LD06 Lidar | [Amazon](https://www.amazon.com/-/es/Sensor-Lidar-LD06-frecuencia-educaci%C3%B3n/dp/B0B4VLQ1M9?th=1) | 63.18 | 1 | 63.18 | 63.18 |
| 1 | Camera |  | SainSmart Wide Angle Fish-Eye Camera for Raspberry Pi | [Amazon](https://www.amazon.es/dp/B00N1YJKFS) | 24.95 | 1 | 24.95 | 24.95 |

## Miscellaneous

| Qty  | Item | Image | Description | Link | Pack Price (€) | Pack Size | Unit Price (€) | Subtotal (€) |
| ---- | --- | --- | --- | --- | --- | --- | --- | --- |
| 0 | [Balance charger](./BOM/battery_charger.md) |  | WANGCL IMAX B6AC Lipo Battery charger B6 80W Digital LCD | [Amazon](https://www.amazon.es/gp/product/B0B3GM8KX9/) | 42.99 | 1 | 42.99 | 0.00 |
| 0 | [NEMA17 stepper motor](./BOM/NEMA17_stepper.md) | | 12V NEMA17 bipolar stepper motor to use with a with L298N driver | [Electronica Embajadores](https://www.electronicaembajadores.com/es/Productos/Detalle/MMPP004/motores-servomotores-actuadores-lineales/motores-paso-a-paso/nema-17-motor-paso-a-paso-12-vcc-ang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) | 12.09 | 1 | 12.09 | 0.00 |
| 0 | [OLED](./BOM/OLED.md) |  | SSD1306 0.96" OLED display | [Amazon](https://www.amazon.es/dp/B09GVTRB2W) | 10.99 | 3 | 3.66 | 0.00 |

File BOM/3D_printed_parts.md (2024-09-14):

## 3D printed parts

### Base plate 

#### Version 2 printed 10/12/23



3D printing took 12h 8' in low quality, 140g after scaling in z to 75% to reduce to 3mm thickness.

Lessons learned: 

* 3mm thickness is enough. Perhaps 4mm is good only where the fixing screws attach the plate to the frame
* 4 screws are enough to fix the plate. Ideally use 10mm M5 screws with phillips or internal hex head and one washer 
* Make open slots instead of holes for ease of installation. 5mm holes are too tight in practice, try 5.2mm
* make raised flanges in the corners of the plate to facilitate aligning the plate to the frame

Next steps: 

* position elements in the plate and holes to fix them.
* make modifications to FreeCAD model

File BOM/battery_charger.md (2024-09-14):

# WANGCL IMAX B6AC Lipo Battery charger B6 80W Digital LCD

Lipo Cargador 11-18V con adaptador para plomo ácido NI-CD/NI-MH 1-6S LI-PO

### Charging the battery

Balance charging the LiPo battery using the iMAX B6AC LiPo balance charger:

| Step | Image | Description |
| ---- | --- | --- |
| 1 |  | Plug the charger to mains to power it up |
| 2 |  | Check that the jacks of the charging cable are correctly connected to the charger (black to negative and red to positive).<br /><br />Connect the XT60 connector of the battery to the charging cable. |
| 3 |  | Insert the JST-XH balance connector of the battery to the designated slot in the balance charger (In our case 3 cells). |
| 4 |  | Use arrows to go to the **Balance Charge** setting.<br /><br />Then Select **LiPo** battery type.<br /><br />Confirm settings. For the 5000mAh 11.1V 50C LiPo battery: **Lipo**,  **3.8A** charging current (below 1C) and **11.1V (3S)** configuration. |
| 5 |  | Hold the **Start** button to start. Press it again to confirm. See [video](./assets/battery_start_charging.MP4) |
| 6 |  | During charging: use arrows to move to the screen with 6 voltages.<br /> **Note:** It is normal to see the lower three indications static at 0.00. This is because the charger is capable of charging batteries with up to 6 cells, but our battery actually has only three.<br />See [video](./assets/battery_while_charging.MP4) |
| 7 | | The charger alarm will beep when charge is complete |

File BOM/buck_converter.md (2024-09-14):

# Buck converter



## Specs

ICQUANZX DC-DC

Voltage: 5-32V input  to 0.8-24V output

Intensity: Max peak 5A, Max. continuous use 3.5A.

Poer: Max power 75W, needs cooling above 50W

Dimensions: ‎11.5 x 7.5 x 2.3 cm

Weight: 30g

## 3D model

* Buck converter (LM2596 is similar): https://grabcad.com/library/buck-converter-lm2596-1

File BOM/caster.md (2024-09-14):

# Caster ball

Ball diameter 0.6" (16mm)



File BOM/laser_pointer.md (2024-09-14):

# Laser pointer

1. Laser Output Type: **Red Point** Laser
2. Dimensions: Diameter: 12mm, Length: 35mm.
3. Weight: 15 gm.
4. Wavelength: 650nm.
5. Voltage: 3~6V.
6. Output Power: Min 2.5mW, Typical 3.0mW, Max 5.0mW.
7. Working current: Min 10mA, Typical 20mA, Max 25mA.
8. Focus can be adjusted with help of lens ring head.

## 3D printed parts

* Laser pointer holder

https://grabcad.com/library/nerf-laserpointer-2-0-1

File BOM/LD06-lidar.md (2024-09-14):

# LD06 Lidar

Weight: 91g

**This file comes from manolobot/ review!!**

cfr: https://articulatedrobotics.xyz/mobile-robot-8-lidar/

2D Lidar manufacturer provides a driver that publishes standard ROS messages of type  `sensor_msgs/LaserScan` with the array of measurements and parameters, including the TF where the Lidar is attached so location of measured points in space can be determined.

Similarly 3D Lidar and depth cameras use `sensor_msgs/PointCloud2`

## References

* LD06 small lidar - How to use the Lidar LD06 ROS2: https://www.youtube.com/watch?v=OJWAsV6-0GE

* LDRobot official page: https://www.ldrobot.com/product/en/98

* The download section https://www.ldrobot.com/download/en/98 used to have Datasheet, Development Manual and SDK (Linux, ROS, ROS2) - luckily copied to /assets folder in this repo

* My repo [Minipupper_fun](https://github.com/mhered/minipupper_fun) has information e.g. PC setup [here](https://github.com/mhered/minipupper_fun/blob/main/MiniPupper_SLAM_Navigation.md) and links [here](https://github.com/mhered/minipupper_fun/blob/main/LD06_Links.md)

## Installing LD06 on RPi

1. Clone and symlink the repo:

```bash
(RPi):$ mkdir ~/git && cd ~/git
(RPi):$ git clone https://github.com/ldrobotSensorTeam/ldlidar_stl_ros2
(RPi):$ ln -s ~/git/ldlidar_stl_ros2/ ~/dev_ws/src/
```

2. Plug the LD06 and find out the device id (`by-id` because the path `/dev/ttyUSB*` may change):

```bash
(RPi):$ ls /dev/serial/by-id
usb-1a86_USB2.0-Ser_-if00-port0
usb-Silicon_Labs_CP2102_USB_to_UART_Bridge_Controller_0001-if00-port0
```

Where `usb-Silicon_Labs_CP2102_USB_to_UART_Bridge_Controller_0001-if00-port0` is the LD06 ( and`usb-1a86_USB2.0-Ser_-if00-port0` is the arduino)

3. Set device permissions:

```bash
(RPi):$ sudo chmod 777 /dev/serial/by-id/usb-Silicon_Labs_CP2102_USB_to_UART_Bridge_Controller_0001-if00-port0
```

4. Edit `ldlidar_stl_ros2/launch/ld06.launch.py` to update `port_name` and build the package and source:

```bash 
(RPi):$ colcon build
(RPi):$ cd ~/dev_ws
(RPi):$ source install/setup.bash
```

Execute with:

```bash
(RPi):$ ros2 launch ldlidar_stl_ros2 ld06.launch.py
```

View it from PC with:

```bash
(PC):$ rviz2
```

## To do

- [ ] copy lidar launch file to manolobot_uno package
- [ ] make config file for rviz for camera and lidar

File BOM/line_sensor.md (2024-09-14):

# Pololu QTR-8RC reflectance sensor array

https://www.pololu.com/product/961



Specs:

- Dimensions: 7.49 x 1.27 x 0.32 cm (without header pins installed)
- Operating voltage: 3.3-5.0 V
- Supply current: 100 mA
- 8 reflectance sensors mounted on a 9.525 mm pitch, 
- Output format: 8 digital I/O-compatible signals that can be read as a timed high pulse
- Optimal sensing distance: 3 mm
- Maximum recommended sensing distance: 9.5 mm
- Weight without header pins:3.09 g

Resources: https://www.pololu.com/product/961/resources

* Arduino library: https://github.com/pololu/qtr-sensors-arduino

* User guide: https://www.pololu.com/docs/0J12

## Tutorial

https://www.youtube.com/watch?v=akTegAQMoxo

Install QTRSensors library in the Arduino IDE

Tutorial with recommendations on how to solder the QTR sensor: https://www.youtube.com/watch?v=C2ZmbrH_bws

Tutorial on using the example from QTRSensors library to test the sensor:

https://www.youtube.com/watch?v=IsQXt-PJ8P0&list=PLqr8J8t_ccS1p8s-B9rlLctFWjpaDeBo1&index=9

```c++
#include <QTRSensors.h>

// This example is designed for use with eight RC QTR sensors. These
// reflectance sensors should be connected to digital pins 3 to 10. The
// sensors' emitter control pin (CTRL or LEDON) can optionally be connected to
// digital pin 2, or you can leave it disconnected and remove the call to
// setEmitterPin().
//
// The setup phase of this example calibrates the sensors for ten seconds and
// turns on the Arduino's LED (usually on pin 13) while calibration is going
// on. During this phase, you should expose each reflectance sensor to the
// lightest and darkest readings they will encounter. For example, if you are
// making a line follower, you should slide the sensors across the line during
// the calibration phase so that each sensor can get a reading of how dark the
// line is and how light the ground is.  Improper calibration will result in
// poor readings.
//
// The main loop of the example reads the calibrated sensor values and uses
// them to estimate the position of a line. You can test this by taping a piece
// of 3/4" black electrical tape to a piece of white paper and sliding the
// sensor across it. It prints the sensor values to the serial monitor as
// numbers from 0 (maximum reflectance) to 1000 (minimum reflectance) followed
// by the estimated location of the line as a number from 0 to 5000. 1000 means
// the line is directly under sensor 1, 2000 means directly under sensor 2,
// etc. 0 means the line is directly under sensor 0 or was last seen by sensor
// 0 before being lost. 5000 means the line is directly under sensor 5 or was
// last seen by sensor 5 before being lost.

QTRSensors qtr;

const uint8_t SensorCount = 8;
uint16_t sensorValues[SensorCount];

void setup()
{
  // configure the sensors
  qtr.setTypeRC();
  qtr.setSensorPins((const uint8_t[]){3, 4, 5, 6, 7, 8, 9, 10}, SensorCount);
  qtr.setEmitterPin(2);

  delay(500);
  pinMode(LED_BUILTIN, OUTPUT);
  digitalWrite(LED_BUILTIN, HIGH); // turn on Arduino's LED to indicate we are in calibration mode

  // 2.5 ms RC read timeout (default) * 10 reads per calibrate() call
  // = ~25 ms per calibrate() call.
  // Call calibrate() 400 times to make calibration take about 10 seconds.
  for (uint16_t i = 0; i < 400; i++)
  {
    qtr.calibrate();
  }
  digitalWrite(LED_BUILTIN, LOW); // turn off Arduino's LED to indicate we are through with calibration

  // print the calibration minimum values measured when emitters were on
  Serial.begin(9600);
  for (uint8_t i = 0; i < SensorCount; i++)
  {
    Serial.print(qtr.calibrationOn.minimum[i]);
    Serial.print(' ');
  }
  Serial.println();

  // print the calibration maximum values measured when emitters were on
  for (uint8_t i = 0; i < SensorCount; i++)
  {
    Serial.print(qtr.calibrationOn.maximum[i]);
    Serial.print(' ');
  }
  Serial.println();
  Serial.println();
  delay(1000);
}

void loop()
{
  // read calibrated sensor values and obtain a measure of the line position
  // from 0 to 5000 (for a white line, use readLineWhite() instead)
  uint16_t position = qtr.readLineBlack(sensorValues);
  
  double position_mm;
  char position_mm_char[10];
  
  // print the sensor values as numbers from 0 to 1000, where 0 means maximum
  // reflectance and 1000 means minimum reflectance, followed by the line
  // position
  for (uint8_t i = 0; i < SensorCount; i++)
  {
    Serial.print(sensorValues[i]);
    Serial.print('\t');
  }
  Serial.print(position);
  Serial.print('\t');
  
  position_mm = ((int)position - 3500)*9.525/1000;
  dtostrf(position_mm, 6, 2, position_mm_char);
  Serial.print("Error: ");
  Serial.print(position_mm_char);
  Serial.println(" mm");
  delay(250);
}
```

During calibration (about 10") move sensor to show full range (e.g. black line and white background). Beware of shades!. LED 13 will turn off when calibration is complete. In serial monitor you can see output: 

```
96 96 96 100 96 96 96 100 
2500 2500 2500 2500 2500 2500 2500 2500 

23	23	0	0	0	23	44	855		7000	Error:  33.34 mm
3	3	24	45	46	362	572	180		5836	Error:  22.25 mm
3	3	24	23	24	362	362	135		5735	Error:  21.29 mm
1	1	23	21	66	249	44	180		5593	Error:  19.94 mm
3	3	24	23	296	227	24	180		5091	Error:  15.15 mm
1	1	1	0	249	159	24	248		5376	Error:  17.87 mm
23	1	1	21	207	1	23	160		5307	Error:  17.21 mm
21	0	0	110	204	0	21	110		4518	Error:   9.70 mm
21	21	0	273	202	0	21	86		3973	Error:   4.51 mm
21	21	21	341	226	1	21	88		3882	Error:   3.64 mm
21	21	21	321	44	0	21	88		3860	Error:   3.43 mm
21	21	66	271	21	0	43	86		3657	Error:   1.50 mm
19	19	362	290	19	19	64	108		3317	Error:  -1.74 mm
43	21	366	110	21	21	43	63		2788	Error:  -6.78 mm
21	89	299	20	0	21	43	20		1770	Error: -16.48 mm
23	412	321	21	0	0	23	0		1437	Error: -19.65 mm
46	252	0	0	0	0	0	0		1000	Error: -23.81 mm
254	48	0	0	0	21	21	20		0		Error: -33.34 mm
209	0	0	0	0	23	23	0		0		Error: -33.34 mm
434	43	21	41	43	89	89	111		2428	Error: -10.21 mm
316	224	21	41	64	88	111	131		2679	Error:  -7.82 mm
23	294	66	41	43	88	109	155		3658	Error:   1.50 mm
23	178	271	43	44	88	111	155		3625	Error:   1.19 mm
219	151	287	218	19	41	41	83		2045	Error: -13.86 mm
21	111	43	273	0	21	21	41		2421	Error: -10.28 mm
66	109	267	613	292	1	1	21		2709	Error:  -7.53 mm
0	0	0	0	252	23	23	21		4000	Error:   4.76 mm
64	21	86	196	637	312	21	0		3759	Error:   2.47 mm
64	0	43	108	133	480	21	0		4147	Error:   6.16 mm
64	0	21	41	88	685	386	20		4982	Error:  14.12 mm
43	0	0	20	66	455	364	20		5336	Error:  17.49 mm
43	0	0	20	43	43	346	20		6000	Error:  23.81 mm
43	0	0	20	64	88	1000406		6121	Error:  24.97 mm
21	0	0	0	21	111	703	1000	6490	Error:  28.48 mm
21	21	21	20	0	0	21	251		7000	Error:  33.34 mm
...
```

Another tutorial: https://www.instructables.com/PID-Based-Line-Following-Robot-With-POLALU-QTR-8RC/

A great video on PID: https://www.youtube.com/watch?v=4Y7zG48uHRo

## 3D model

SLDPRT downloaded from grabcad: https://grabcad.com/library/qtr8a-sensor-pololu-1 , converted with On Shape

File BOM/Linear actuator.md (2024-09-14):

# Linear actuator



## 3D part

* Power door lock motor (12V car door actuator): https://grabcad.com/library/power-door-lock-motor-1

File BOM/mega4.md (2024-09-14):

# UUGEAR MEGA4 - 4-Port USB Hub

The UUGear MEGA4 is a 4-Port USB 3.1 PPPS (Per-Port Power Switching) hub designed for theRPi

adds 4 USB 3.1 ports

power on each USB port can be individually turned on/off  via software or via UUGear Web Interface (UWI) on PC, Tablet or Smartphone. This allows resetting devices or saving energy (e.g. the Lidar)

can be externally powered connecting a 5V power supply to its  USB-C connector to increase its current output ability up to 5A, and 2.5A per port

there is a protection to prevent the hub from back-powering the RPi.

## Install software

The software is needed to turn on/off the power on each USB port.

Download and run the installation script to install the software in `mega4` directory and the UUGear Web Interface (UWI) in `uwi` directory in the RPi:

```bash
(RPi):$ wget https://www.uugear.com/repo/MEGA4/install.sh
(RPi):$ sudo sh install.sh
```

Note: `sudo` is needed to run the script because it attempts to disable USB auto-suspend in `/boot/cmdline.txt`.

After installing the software, reboot the RPi so the UWI server will run in the background. 

With the default  configuration you should be able to access the MEGA4 via UWI on address https://raspberrypi:8000/mega4/ (Note:???)

## Specs

* Dimensions: 85 x 56 x 9 mm (USB plug protrudes 7mm)

* Weight: 60g (29g without accesories)

* Output Current

  - Bus-powered only: up to 1.2A in total (limited by Raspberry Pi 4B)

  - With supplemental power supply: up to 5A in total, and 2.5A per port (also depends on the power supply)

## References

https://www.uugear.com/product/mega4-4-port-usb-3-ppps-hub-for-raspberry-pi-4b/

https://thepihut.com/products/mega4-4-port-usb-3-1-ppps-hub-for-raspberry-pi-4

https://www.uugear.com/doc/MEGA4_UserManual.pdf

The software is a wrapper of utility uhubctl: https://github.com/mvp/uhubctl

## First try to switch off Lidar

1. install `uhubctl`:

```bashç
(RPi):$ sudo apt install uhubctl
```

2. find devices:

```bash
(RPi):$ sudo uhubctl
Current status for hub 2-2 [2109:0817 VIA Labs, Inc. USB3.0 Hub, USB 3.10, 4 ports]
  Port 1: 02a0 power 5gbps Rx.Detect
  Port 2: 02a0 power 5gbps Rx.Detect
  Port 3: 02a0 power 5gbps Rx.Detect
  Port 4: 02a0 power 5gbps Rx.Detect
Current status for hub 2 [1d6b:0003 Linux 5.4.0-1079-raspi xhci-hcd xHCI Host Controller 0000:01:00.0, USB 3.00, 4 ports]
  Port 1: 02a0 power 5gbps Rx.Detect
  Port 2: 0263 power 5gbps U3 enable connect [2109:0817 VIA Labs, Inc. USB3.0 Hub, USB 3.10, 4 ports]
  Port 3: 02a0 power 5gbps Rx.Detect
  Port 4: 02a0 power 5gbps Rx.Detect
Current status for hub 1-1.2 [2109:2817 VIA Labs, Inc. USB2.0 Hub, USB 2.10, 4 ports]
  Port 1: 0103 power enable connect [0eef:0005 WaveShare ws170120 WaveShare ws170120]
  Port 2: 0103 power enable connect [10c4:ea60 Silicon Labs CP2102 USB to UART Bridge Controller 0001]
  Port 3: 0103 power enable connect [1a86:7523 USB2.0-Ser!]
  Port 4: 0100 power
Current status for hub 1 [1d6b:0002 Linux 5.4.0-1079-raspi xhci-hcd xHCI Host Controller 0000:01:00.0]
  Port 1: 0503 power highspeed enable connect [2109:3431 USB2.0 Hub, USB 2.10, 4 ports]
```

3. switch off (but does not seem to work):

```bash
(RPi):$ sudo uhubctl -a off -l 1-1.2 -p 2
Current status for hub 1-1.2 [2109:2817 VIA Labs, Inc. USB2.0 Hub, USB 2.10, 4 ports]
  Port 2: 0103 power enable connect [10c4:ea60 Silicon Labs CP2102 USB to UART Bridge Controller 0001]
Sent power off request
New status for hub 1-1.2 [2109:2817 VIA Labs, Inc. USB2.0 Hub, USB 2.10, 4 ports]
  Port 2: 0000 off
```

## 3D model

Not available so I made one, and uploaded it to grabCAD, see: https://grabcad.com/library/uugear-mega4-4-port-usb-3-1-ppps-hub-for-raspberry-pi-4b-1

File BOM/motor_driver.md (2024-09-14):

# L298N Motor driver

 Dimensions: ‎ 5 x 5 x 3 cm

Weight: 27 grams 

Motor output voltage	5V – 35V
Motor output voltage (Recommended)	7V – 12V
Logic input voltage	5V – 7V
Continuous current per channel	2A
Max Power Dissipation	25W

## Tutorials

* [Interface L298N DC Motor Driver Module with Arduino](https://lastminuteengineers.com/l298n-dc-stepper-driver-arduino-tutorial/)

* [L298N Motor Driver – Arduino Interface, How It Works, Codes, Schematics](https://howtomechatronics.com/tutorials/arduino/arduino-dc-motor-control-tutorial-l298n-pwm-h-bridge/)

* [How to use the L298N Motor Driver ](https://create.arduino.cc/projecthub/ryanchan/how-to-use-the-l298n-motor-driver-b124c5)

## Pinout

motor_driver_wiring

motor_driver_wiring

motor_driver_wiring

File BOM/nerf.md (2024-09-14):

# Nerf

Inspiration from:

* https://www.youtube.com/watch?v=4pb9OxdDGfk
* https://www.instructables.com/How-to-Make-a-Human-Seeking-Nerf-Auto-Turret-Robot/
* DIY Autonomous Nerf Turret: https://www.youtube.com/watch?v=Xz5ZvW98HRs
* How to Make a Raspberry Pi Motion Tracking Airsoft / Nerf Turret: https://www.youtube.com/watch?v=HoRPWUl_sF8&t=1327s
* You Can't Hide from the Face Tracking Nerf with AI: https://www.youtube.com/watch?v=bPh1TztVlwk

We rushed in to buying the Commander, then realised loading the spring automatically would probably require an expensive linear actuator of the kind used for garage doors, and the sequence would be difficult to implement, heavy and impractical.

Then we did a proper review of the options and the Stryfe appears to be the best candidate, followed by the Ultra 2.

| Image | Model | Hasbro Ref. | Dimensions | Weight | Price  | Comments |
| --- | --- | --- | --- | --- | --- | --- |
|  | Nerf Elite 2.0 Commander RD-6 | E9485EU5 | 6.7 x 36.2 x 24.1 cm | 560g | 9.99€  | Reloading with the black slider while keeping the trigger pressed allows rapid fire. However the slider has ~60cm stroke and the spring requires a lot of force. |
|  | Nerf Ultra 2 | E79214R00 | 7.9 x 36.8 x 24.1 cm | 490g (probably not including batteries)<br />6 AA batteries ~140g | 34.98€ | Easier to automate: keep lower trigger pressed continuously and actuate the top one with a 12V standard car door actuator. However there are bad reviews due to inaccurate Ultra darts and frequent clogging. |
|  | Nerf Modulus Stryfe | C3583F03 | 7.3 x 25.7 x 42.2 cm | 930g (?? Possibly including attachments)<br/>4 AA batteries ~100g | 42.07€ | Easy to automate, same as the Ultra 2. Pricier but has better reviews. Heavier? Check dimensions... |

## 3D parts

* Nerf rail: https://grabcad.com/library/nerf-rail-modelled-after-a-stryfe-1 (not used)

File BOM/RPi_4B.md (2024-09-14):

# Raspberry Pi 4B





## Soft reset / soft power down button

1. install `pip` in the RPi and then install the [RPi.GPIO](https://pypi.org/project/RPi.GPIO/) package. **Note: with `sudo` so later it will be accessible by `root`  and the python script will run from `/etc/rc.local`**:

```bash
(Rpi):$ sudo apt install python3-pip
(Rpi):$ sudo pip install RPi.GPIO
```

2. To avoid [this error](https://raspberrypi.stackexchange.com/questions/40105/access-gpio-pins-without-root-no-access-to-dev-mem-try-running-as-root), add the user to the `gpio` group and check that the device file `/dev/gpiomem` has the correct permissions:

```bash
(RPi):$ sudo adduser mhered gpio
(Rpi):$ ls -l /dev/gpiomem
crw-rw---- 1 root gpio 244, 0 Dec 28 22:51 /dev/gpiomem
```

	If it doesn't, then set the correct permissions as follows

```bash
(Rpi):$ sudo chown root.gpio /dev/gpiomem
(Rpi):$ sudo chmod g+rw /dev/gpiomem
```

	This needs to be repeated after every reboot so we will add these commands to the end of `/etc/rc.local` 

3. Wire the button to pins 9 (GND) and 11 (GPIO17 - INPUT). Note that the input pin is pulled HIGH by default so pushing it yields LOW.

4. Write the python script that listens for the button: [../code/button/safe_shutdown.py](../code/button/safe_shutdown.py) **This link does not work because it is in manolobot/ FIX!**

	For more details on wiring and the script refer to:

* https://www.electroniclinic.com/how-to-reset-or-shutdown-raspberry-pi-using-a-button/

* https://learn.sparkfun.com/tutorials/raspberry-pi-safe-reboot-and-shutdown-button/all
* https://www.ridgesolutions.ie/index.php/2013/02/22/raspberry-pi-restart-shutdown-your-pi-from-python-code/
* https://raspberrypi.stackexchange.com/questions/69194/using-gpiozero-button-for-2-functions-long-short-press

5. Create `/etc/rc.local`:

```bash
#!/bin/sh -e
#
# File /etc/rc.local
# created by MH on 28.01.2023
#
# This script is executed at the end of each multiuser runlevel.
# Ensure that the script will "exit 0" on success or any other
# value on error.
#
# To enable or disable this script, just change the execution
# bits.
#
# By default, this script does nothing.

# Set permissions for dev/gpiomem
chown root.gpio /dev/gpiomem
chmod g+rw /dev/gpiomem

# run in the background the script that listens for the safe reset/shutdown button
/usr/bin/python3 /home/mhered/manolobot/code/button/safe_shutdown.py &

exit 0
```

5. Give it execution permission:

```bash
(Rpi):$ sudo chmod +x /etc/rc.local
```

Sources on playing with `/etc/rc.local`:

* https://learn.sparkfun.com/tutorials/how-to-run-a-raspberry-pi-program-on-startup 
* https://linuxhint.com/use-etc-rc-local-boot/

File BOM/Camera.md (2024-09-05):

# SainSmart Wide Angle Fish-Eye Camera for Raspberry Pi

Sensor Omnivision 5647
FOV 160

## Specs (Amazon)

Módulo de cámara Omnivision 5647 de 5 MP. 
\- Resolución de imagen silenciosa: 2592 x 1944. 
\- Ángulo de visualización: 160 grados. 
\- Ángulo de la cámara: el tamaño se puede reemplazar. 
\- Vídeo: Soporta 1080p a 30 fps, 720p a 60 fps y 640 x 480 p 60/90 grabación de 15 pines interfaz serie de cámara MIPI 
\- Tamaño: aprox. 25 x 24 x 9 mm.

## HFOV from angle (source ChatGPT)

HFOV =tan(angle/2) = tan(160 deg / 2) ~=  5.671

## CAD files 

* https://grabcad.com/library/raspberry-pi-camera-ov5647-1 wrong dimensions
* https://grabcad.com/library/sainsmart-noir-camera-module-fov-175-wide-angle-lens-for-raspberry-pi-1 SLDPRT only
* https://grabcad.com/library/rpi-camera-m-fisheye-lens-1

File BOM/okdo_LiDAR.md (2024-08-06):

# LetsOKdo LiDAR HAT for Raspberry Pi kit

cfr this [Getting started guide](./assets/A700000007824693.pdf), downloaded from [here](https://www.pi-shop.ch/lidar-ld06-lidar-module-with-bracket-entwicklungskit-fuer-raspberry-pi-sbc) 

The kit comes with cables for GPIO header pins and a ROS 1 driver: https://github.com/LetsOKdo/ld19

I bought this [CP2102 USB to TTL adapter](https://www.amazon.es/gp/product/B07N2YLH26/) and connected it iaw the following diagram (source is this [LD19_Development_Manual V2.3](./assets/LD19_Development Manual_V2.3.pdf), downloaded from [here](https://www.elecrow.com/download/product/SLD06360F/LD19_Development%2520Manual_V2.3.pdf) ).



| CP2102 USB to TTL adapter | LD06 LiDAR (#1-4 from left to right) |
| --- | --- |
| 3V3 | |
| TXD | |
| RXD | #1 (white) |
| GND | #3 (red) |
| +5V | #4 (blue) |

Note: yellow cable #2  (PWM?) is not connected

More info on this [LDROBOT_LD06_Datasheet](./assets/LDROBOT_LD06_Datasheet.pdf), downloaded from [here](https://www.inno-maker.com/product/lidar-ld06/)

## ROS2 driver

I used the same driver I had for manolobot and it worked, cfr [instructions in the repo](https://github.com/mhered/manolobot/blob/main/BOM/LD06-lidar.md)

In RVIZ (found by trial and error, not endorsed): 

- Fixed Frame: base_laser
- Add LaserScan
- Topic: /scan

### Other ROS2 drivers for LD06/19 available on Github

* [Myzhar/ldrobot-lidar-ros2](https://github.com/Myzhar/ldrobot-lidar-ros2)

* [linorobot/ldlidar](https://github.com/linorobot/ldlidar/tree/ros2) - an attempt to fix and improve the driver provided by LDRobots in their [website](https://www.ldrobot.com/download/44)

* [ldrobotSensorTeam/ldlidar_ros2](https://github.com/ldrobotSensorTeam/ldlidar_ros2)

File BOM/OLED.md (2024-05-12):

# SSD1306 OLED 

Tutorial (in Spanish): https://www.youtube.com/watch?v=cWgWvNhWg-A&t=10s

SSD1306 is a popular controller for OLED screens

 resolution 128x64

I2C communication requires only 4 pins: GND, VCC and 

SDA > A4

SCL > A5

Install libraries : Adafruit SSD1306 + dependencies (adafruit GFX library: a graphical library)

There is a demo example

Check if the I2C address is 0x3D or 0x3C

Boilerplate code:

```c++
#include <Wire.h> // I2C comms
#include <Adafruit_GFX.h> // graphical library
#include <Adafruit_SSD1306.h> // SSD1306 controller library

#define SCREEN_WIDTH 128 // OLED display width, in pixels
#define SCREEN_HEIGHT 64 // OLED display height, in pixels

// Declaration for an SSD1306 display connected to I2C (SDA, SCL pins)
// The pins for I2C are defined by the Wire-library.
// For arduino UNO or NANO:       A4(SDA), A5(SCL)
#define OLED_RESET     -1 // Reset pin # if screen has 5th wire (or -1 otherwise)
#define SCREEN_ADDRESS 0x3C // try 0x3D or 0x3C
// create instance of display
Adafruit_SSD1306 display(SCREEN_WIDTH, SCREEN_HEIGHT, &Wire, OLED_RESET); // &Wire is pointer to I2C comms

void setup() {
  // initialize serial port at 9600 bauds
  Serial.begin(9600);

  // initialize screen
  // SSD1306_SWITCHCAPVCC to generate internally 3.3V to power the display or SSD1306_EXTERNALVCC to power it externally
  if (!display.begin(SSD1306_SWITCHCAPVCC, SCREEN_ADDRESS)) {
    Serial.println(F("SSD1306 allocation failed"));
    for (;;); // Loop forever
  };

  display.clearDisplay(); // clear screen
  display.setTextSize(2); // 1 - 7... (1: 4x8pix, 2: 8x16pix, ...) 
  display.setTextColor(WHITE);
  display.setCursor(3, 1); // top left origin in pixels
  display.println("HELLO");
  display.setCursor(5, 17); // top left origin in pixels
  display.println("WORLD!");
  display.display(); //draw

}
void loop() {};

```

Power consumption: according to https://bitbanksoftware.blogspot.com/2019/06/how-much-current-do-oled-displays-use.html,  for text (~50% pixels at 100%) is around 10mA so at 5V is ~50mW 

## Useful references

* A tool to design pixelart: https://www.pixilart.com/



* Check out wokwi online emulator https://wokwi.com/ for Arduino, ESP32 and Raspberry Pi Pico and animation maker https://animator.wokwi.com/

  Using the wokwi emulator I made code to display distance measurements, check:

  * parking_sensor: https://wokwi.com/projects/380210366387901441
  * distance_measurement: https://wokwi.com/projects/380210201131269121

* Check out also this image2cpp tool to make byte arrays from images and viceversa: http://javl.github.io/image2cpp/

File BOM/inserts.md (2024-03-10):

# Heat set inserts



Couldn't find a data sheet for the inserts I bought

Video tutorial: https://www.youtube.com/watch?v=P7nHyI1TwKY

* check the data sheets for maximum diameter and thickness
* insert them from the opposite side where you are going to screw 
* set the soldering iron 50-100C hotter than the nozzle temperature of the 3D printer
* keep soldering iron aligned with the insert 
* be patient, the slower it goes in, the better the bond
* remove iron when the insert is flush

## A table of hole sizes from other brand



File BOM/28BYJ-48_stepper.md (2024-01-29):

# 12V 28BYJ-48 Stepper motor / ULN2003A-based driver board



Stepper motor 28BYJ-48 with ULN2003A based driver board. 

The board can be connected directly to a microcontroller and controls the motor by sending alternating pulses to the motor coils. The onboard LEDs indicate which coils/outputs are active. 

* Supply voltage: 12VDC
* Dimensions (driver): 29 x 21mm
* Dimensions (motor): ø28x19mm
* Poles: 4 (unipolar)
* Gear ratio: 64:1
* Step angle: 5.625° (/64)
* Steps per rev.: 4096
* DC resistance: 200ohm (±7%)
* Shaft: 5mm flat

Data sheet 12V: https://electronperdido.com/wp-content/uploads/2018/08/28BYJ-12V-datasheet.pdf

Data sheet 5V: https://www.makerguides.com/wp-content/uploads/2019/04/28byj48-Stepper-Motor-Datasheet.pdf

Two basic tutorials (refer to 5V motor):

https://www.makerguides.com/28byj-48-stepper-motor-arduino-tutorial/

https://lastminuteengineers.com/28byj48-stepper-motor-arduino-tutorial/

Joystick + Stepper Elegoo tutorial with code:  https://www.youtube.com/watch?v=5WTLD2XcL5A&t=101s

Understanding joysticks tutorial: https://www.youtube.com/watch?v=B6YEQj4d5WU

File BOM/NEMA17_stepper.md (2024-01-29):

# NEMA17 Stepper motor

12V 200 steps per revolution NEMA17 motor without datasheet (MMPP004 @ Electronica Embajadores)

Source DroneBot Workshop: https://www.youtube.com/watch?v=0qwrnUeSpYQ

## Unipolar vs bipolar

| Unipolar | Bipolar |
| --- | --- |
| 4 wire | 5 or 6 wires |
| needs voltage reversal | no voltage reversal |
| Higher torque | Lower Torque |
| Lower Max Speed | Higher Max Speed |
| Requires a more Advanced Controller | Simpler Controller  |

## Selecting a Stepper AKA stepper specs

- Step Angle: in degrees per step or steps per revolution
- Voltage rating
- Current rating
- Coil Resistance
- Inductance: relates to max speed, the higher the slower the motor
- Holding Torque:  max torque when energized
- Detent or Residual Torque: torque when not energized
- Shaft style: round, D, geared, Lead-Screw

## Wiring of a NEMA stepper without diagram

1. Identify the matching pairs checking for continuity with the multimeter
2. Determine the polarity of the two pairs by trial and error using the sample code from `Stepper.h` that can be found in Examples, i.e. until clockwise/counterclockwise work fine in `stepper_oneRevolution` and all steps are in the same direction in `stepper_oneStepAtATime`

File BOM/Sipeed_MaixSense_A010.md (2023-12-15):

# Sipeed MaixSense A010 

## Downloads (specs, CAD, SDK, dwgs)

https://dl.sipeed.com/shareURL/MaixSense/MaixSense_A010

## Official Wiki

https://wiki.sipeed.com/hardware/en/maixsense/maixsense-a010/maixsense-a010.html

100x100 pixels 

2.5m range

3D ToF sensor

3D point clouds ROS1 and ROS2

USB FS

UART protocol

## Official repo

https://dl.sipeed.com/shareURL/MaixSense/MaixSense_A010

* CAD files
* Data sheet
* SDK
* drawings

## Install comtool

comtool repo: https://github.com/sipeed/MetaSense-ComTool

Installation:

Check out @JRBowling twitter thread from 24/11/23 onwards fighting with the SDK

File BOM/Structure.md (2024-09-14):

# Structure

Inspiration: Simon robot: https://github.com/simonllopez/mini_robot_hw ( see https://esimonsite.com/proyectos/mini_robot/)

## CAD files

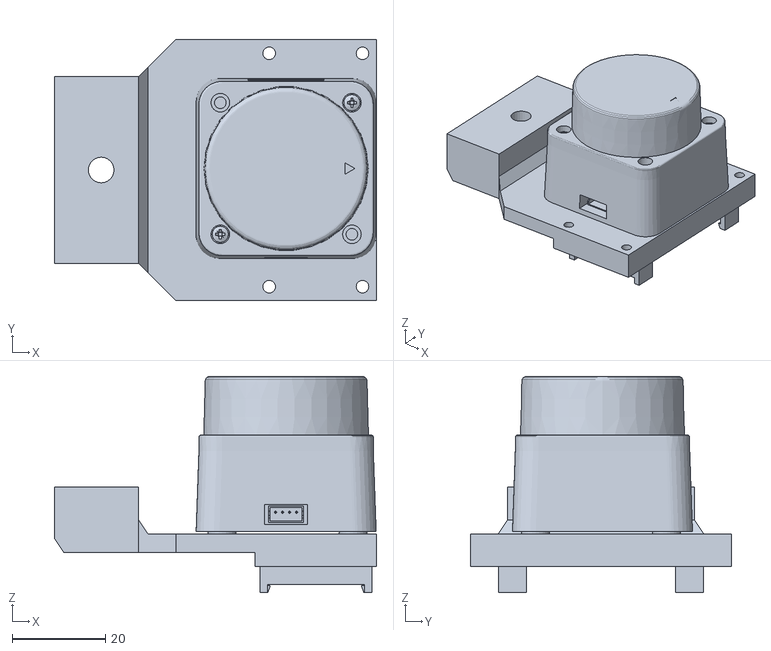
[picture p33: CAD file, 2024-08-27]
sevillabot/meshes/ADDON_Lidar_assy.stl
69.0 x 56.0 x 46.4

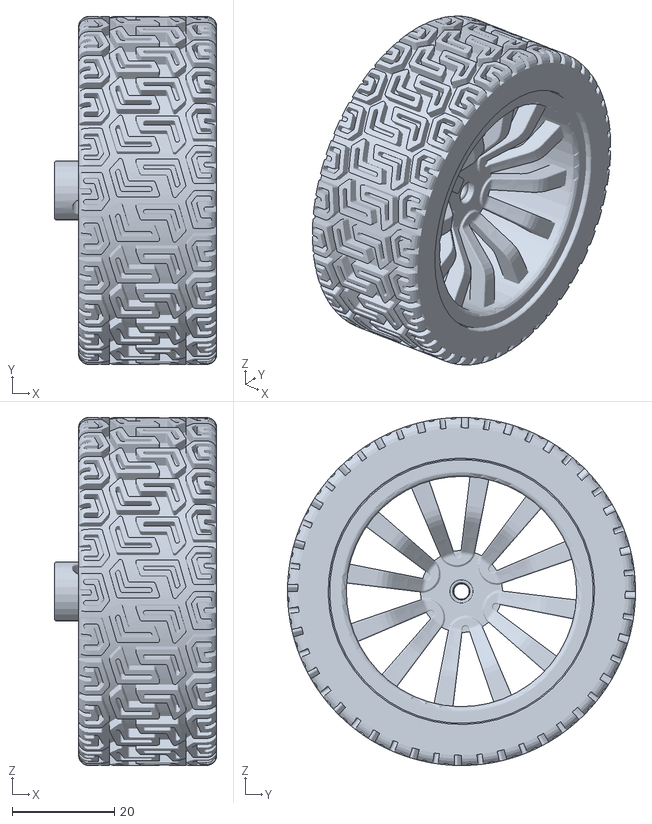
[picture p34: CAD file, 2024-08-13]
sevillabot/meshes/ASSY_Wheel.stl
31.8 x 68.0 x 68.0

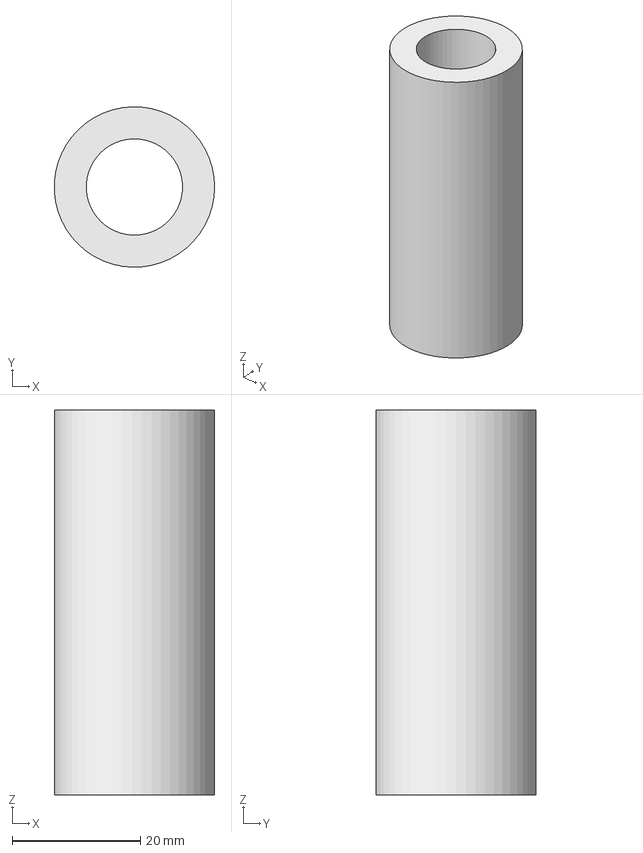
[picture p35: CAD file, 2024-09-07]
inertial/assets/bushing.FCStd
25.0 x 25.0 x 60.0 mm

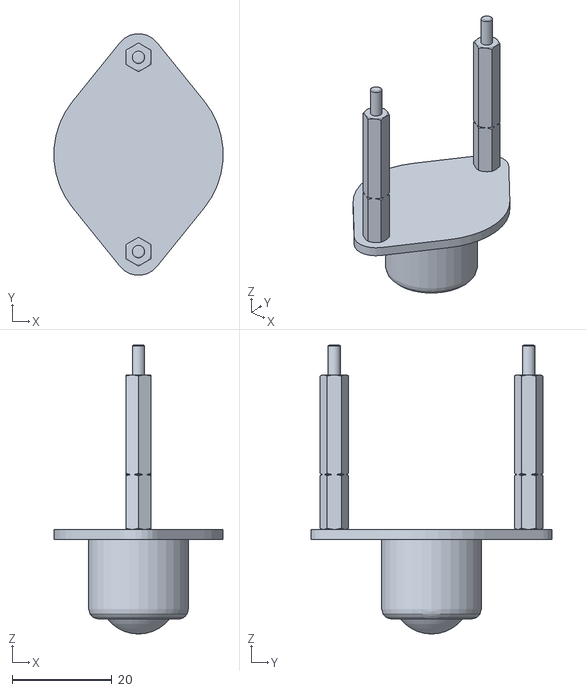
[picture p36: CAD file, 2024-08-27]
sevillabot/meshes/ADDON_caster_wheel.stl
33.9 x 48.4 x 58.0

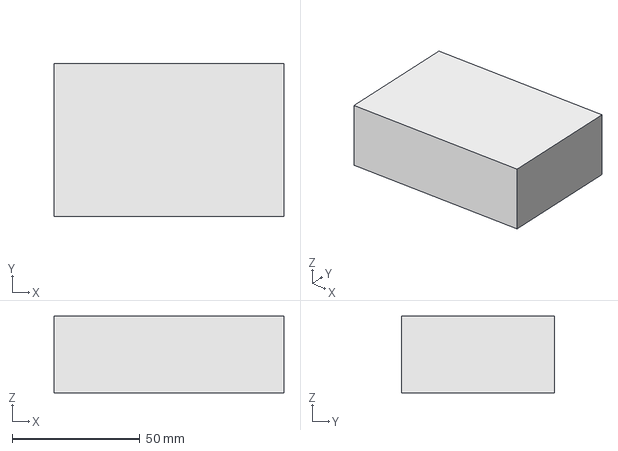
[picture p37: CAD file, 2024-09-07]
inertial/assets/box_90x60x30.FCStd
90.0 x 60.0 x 30.0 mm

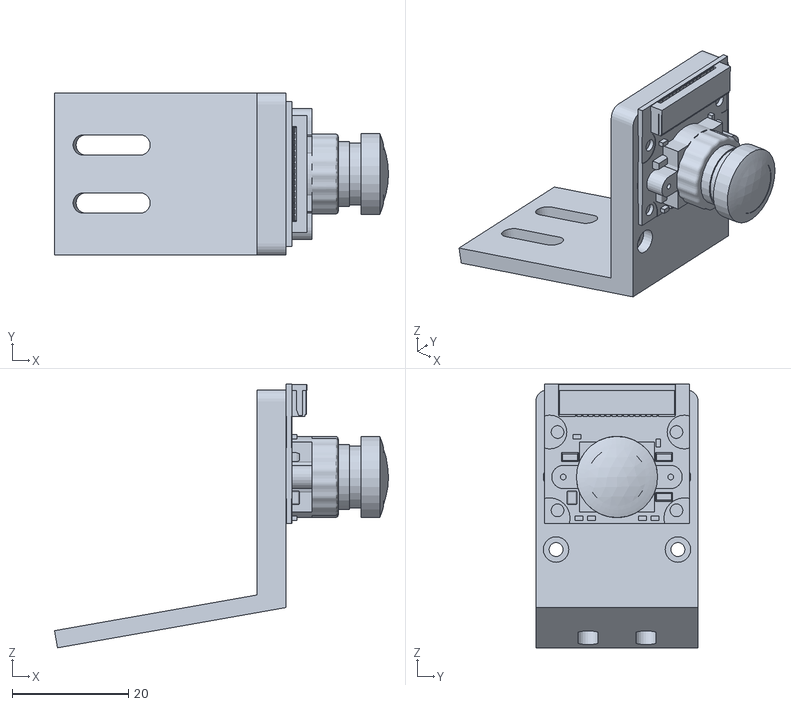
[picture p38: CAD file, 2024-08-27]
sevillabot/meshes/ADDON_front_camera.stl
57.6 x 28.0 x 45.4

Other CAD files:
inertial/assets/box_90x60x30.stl
inertial/assets/bushing.stl

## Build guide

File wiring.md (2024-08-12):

# Motor Wiring

Note: kept L298N jumper on instead of piggybacking 5V from Arduino

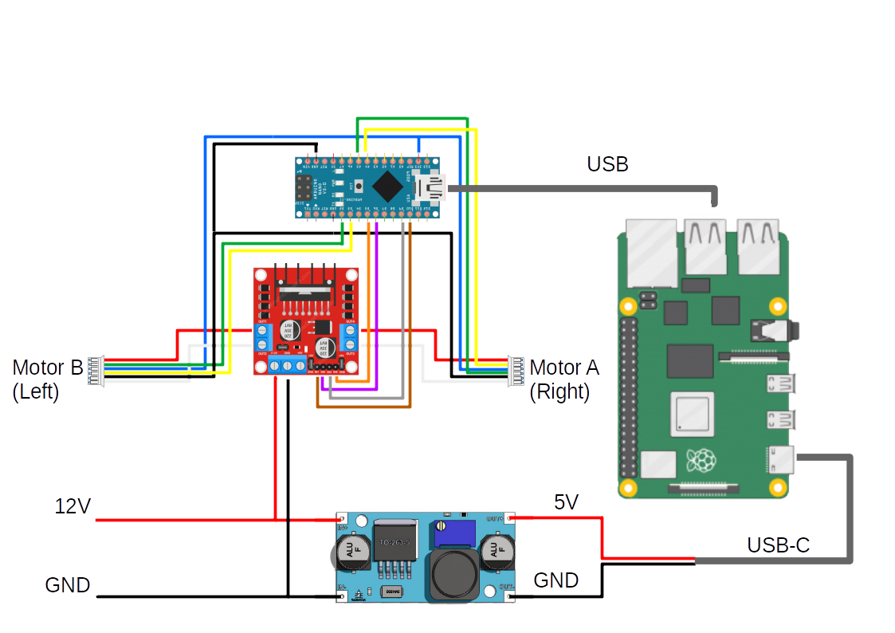
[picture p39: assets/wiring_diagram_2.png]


| L298 | Arduino | Motor | Color  |
| ---- | --- | --- | --- |
| out1 | | motor B (left) red | red |
| out2 | | motor B (left) white | white  |
| out3 | | motor A (right) white  | white  |
| out4 | | motor A (right) red | red |
| n1 | D10 | | brown  |
| n2 | D6 | | purple |
| n3 | D9 | | grey |
| n4 | D5 | | orange |
| | D3 | motor B (left) yellow  | yellow |
| | D2 | motor B (left) green | green  |
| | A5 | motor A (right) yellow | yellow |
| | A4 | motor A (right) green  | green  |

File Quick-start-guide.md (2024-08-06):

# Quick Start Guide

## Start sevillabot

### Charge the battery

Balance charging the LiPo battery using the iMAX B6AC LiPo balance charger:

1.  Plug the charger to mains to power it up
2. Check that the jacks of the charging cable are correctly connected to the charger (black to negative and red to positive). 
3.  Connect the XT60 connector of the battery to the charging cable. 
4.  Insert the JST-XH balance connector of the battery to the designated slot in the balance charger (In our case 3 cells). 
5.  Use arrows to go to the **Balance Charge** setting.
6.  Select **LiPo** battery type. 
7. Confirm settings. For the 5000mAh 11.1V 50C LiPo battery: **Lipo**,  **3.8A** charging current (below 1C) and **11.1V (3S)** configuration. 
8.  Hold the **Start** button to start. Press it again to confirm. 
9. During charging: use arrows to move to the screen with 6 voltages. It is normal to see the lower three indications static at 0.00. This is because the charger is capable of charging batteries with up to 6 cells, but our battery actually has only three.
10. The charger alarm will beep when charge is complete

### Switch on the robot

Red switch on the side from **O** to **I**

### Spawn the robot

SSH into the robot , source ROS2 workspace and spawn the robot:

```bash
(PC T1)$ ssh mhered@sevillabot
mhered@192.168.8.170's password: 
...
(bot T1)$ cd ~/robot_ws/
(bot T1)$ source install/setup.bash
(bot T1)$ ros2 launch sevillabot launch_robot.launch.py
```

Note: After the modification made to the launch file, this now spawns the robot, launches `twist_mux` and launches the gamepad launcher `joystick.launch.py` .

Shortcurt:

```bash
$ cd ~/sevillabot/commands
$ . activate_bot.bash
```

### Move the robot

(**Note: this step is no longer needed, it is already included in the robot launch file**). 

To control only robot the base: ssh into RPi, source and launch launch gamepad controller:

```bash
(PC T2)$ ssh mhered@sevillabot
mhered@192.168.8.170's password: 
...
(bot T2)$ cd ~/robot_ws/
(bot T2)$ source install/setup.bash
(bot T2)$ ros2 launch sevillabot joystick.launch.py
```

The controls are defined in a parameter file which implements:

- Dead man switches: LB button (left shoulder) for normal speed, RB button (right shoulder) for turbo
- Control on left stick: vertical axis for forward/backward motion and horizontal axis for rotation.

#### Gamepad Logitech F710 from bot (default)

1. Connect gamepad USB dongle to RPi top left USB port (to free reserved ports to Arduinos)
2. Ensure gamepad mode is set to **X** (check switch in front face of gamepad)

#### Binbok wireless from PC

Connect the gamepad to PC in Ubuntu:

* ensure it is charged (or charge with microUSB)
* to pair press HOME + SHARE (small button labelled 'S' on the left above the cross) until light flashes white (note if you press HOME + 'O' button on the right the white light blinks, not flashes)
* In Bluetooth settings select Wireless Controller to Connect. Light stops flashing and turns blue
* You may want to test it works with `$ evtest`

#### With keyboard from PC

This is an alternative (for base robot only) if no gamepad is available. 

Launch keyboard teleop controller in PC:

```bash
(PC T2)$ ros2 run teleop_twist_keyboard teleop_twist_keyboard --ros-args -r /cmd_vel:=/cmd_vel_joy
```

Note remapping of topic `/cmd_vel` to `/cmd_vel_joy` (before was `/diff_cont/cmd_vel_unstamped` but this changed after using `twist_mux`)

Now you can move the robot from computer with the keyboard and see it in RVIZ!

Note: keyboard controls for addons are implemented only partially, see `code/command_claw.py` and `code/command_gun.py`

## Control addons

To control also addons, ssh again into RPi, source and launch `joy_subscriber` node:

```bash
(PC T3)$ ssh mhered@sevillabot
mhered@192.168.8.170's password: 
...
(bot T3)$ cd ~/robot_ws/
(bot T3)$ source install/setup.bash
(bot T3)$ ros2 launch sevillabot joy_subscriber.py
```

- For zombie challenge: 
  - Y button to toggle laser target
  - X to fire 
  - Digital pad UP / DOWN to adjust aim up or down
- For Eco disaster
  - Digital pad LEFT / RIGHT to open and close the claw

### Launch RVIZ with config file in the PC

Source ROS2 workspace in PC and launch RVIZ:

```bash
(PC T4)$ cd ~/dev_ws/
(PC T4)$ source install/setup.bash
(PC T4)$ rviz2 -d ~/dev_ws/src/sevillabot/config/bot_with_sensors.rviz
```

Note we use a predefined config file but it is not necessary

### Sensors

#### Stream camera images

SSH to the robot from another Terminal and launch the camera controller:

```bash
(PC T5)$ ssh mhered@sevillabot
mhered@192.168.8.170's password: 
...
(bot T4)$ cd ~/robot_ws/
(bot T4)$ source install/setup.bash
(bot T4)$ ros2 launch sevillabot camera.launch.py
```

#### Stream LiDAR scans

Launch the LIDAR controller:

```bash
(bot T5)$ cd ~/robot_ws/
(bot T5)$ source install/setup.bash
(bot T5)$ ros2 launch sevillabot ld06.launch.py 
```

#### Monitor from PC

RVIZ shows LiDAR. Try Orthographic View.

```bash
(PC T6)$ rviz2 -d ~/dev_ws/src/sevillabot/config/bot_with_sensors.rviz
```

In RVIZ Add Camera and select topic `/image_raw/compressed`

It does not show the camera feed in RVIZ as it should... BUT it works with RQT:

```bash
(PC T6)$ cd ~/dev_ws/
(PC T6)$ source install/setup.bash 
(PC T6)$ ros2 run rqt_image_view rqt_image_view
```

#### 

## Power off sevillabot

```bash
$ sudo shutdown -h now
```

Wait a bit for RPi to power down before switching off mains red button.

**NOT YET IMPLEMENTED**

Safe reset and shutdown: the blue button.

* Shortly pressing the Blue button is ignored (considered noise)
* ~1 sec press resets the RPi (not sure if there is a use case for this)
* 4 sec press shuts down safely the RPi

After Lidar powers off (means RPi powered off) switch off mains red button

See implementation in file `safe_shutdown.py` in: [](/home/mhered/manolobot/code/button/) 

## To Do

- [x] copy code over to sevillabot and update calls

ISSUES CREATED

* ** calibrate for sevillabot robot dimensions

* ** read addon controls from the `joystick.yaml` param file 

- [ ] ** optimize controls. e.g. move left-right to right joystick?
- [ ] ** integrate `joy_subscriber` in the joystick launch file to control gun and clamp addons ??
- [ ] add photos / video of battery charging
- [ ] fix issue with camera in RVIZ
- [ ] implement power down button making it more usable (remove short press for reset and provide feedback for shutdown)
- [ ] wheels skid, big time
- [ ] motors have a lot of hysteresis

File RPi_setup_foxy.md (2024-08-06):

# Raspberry Pi 4B 4Gb setup for ROS2 Foxy

## Install ubuntu MATE 20.04 

ROS2 Foxy requires Ubuntu 20.04 (or derivative)

1. Buy a 64Gb microSD card (as recommended here: https://ubuntu-mate.org/raspberry-pi/).
2. Format the SD card FAT32, e.g. using `gparted` in the ubuntu GUI

### First few failed attempts

1. Download the Ubuntu MATE 20.04.01 arm64 image: `ubuntu-mate-20.04.1-desktop-arm64+raspi.img.xz` from here: https://releases.ubuntu-mate.org/20.04/arm64/ 

2. You may want to verify the checksum of the download with `$ sha256sum ubuntu-mate-20.04.1-desktop-arm64+raspi.img.xz` (should match the content of `ubuntu-mate-20.04.1-desktop-arm64+raspi.img.xz.sha256`)

3. Flash the image onto the card using e.g. https://etcher.balena.io/. This is reasonably fast.

4. Insert the SD card in the RPi, connect it to a keyboard, mouse, screen and power, switch it on, and follow the steps of the Ubuntu MATE OS setup process. 

   Initially boot did not start and complained that `start_x.elf` was not compatible and needed newer software. Turns out RPi 4 apparently required a firmware update (Not sure why, the board is dated 2018...??).

   To fix it: copy manually all files `start*.elf` and `fixup*.dat` from this repo https://github.com/raspberrypi/firmware/tree/master/boot to the boot partition in the SD, following this PDF guide: https://pip.raspberrypi.com/categories/685/documents/RP-003476-WP/RP-003476-WP-1.pdf to update the firmware which I found in this forum: https://forums.raspberrypi.com/viewtopic.php?t=346302

   This allowed me to progress a bit but OS installation crashed during keyboard setup. I tried many things over several days, but eventually I gave up and started again from scratch.

   ### The good way to install ubuntu MATE 20.04 on RPi 4B

   According to this: https://askubuntu.com/questions/1348560/is-ubuntu-20-04-desktop-for-raspberry-pi-4-no-longer-available the proper way to install Ubuntu 20.04 desktop is installing ubuntu 20.04 server first then installing the desktop on top.

   1. Install ubuntu 20.04 server following the official instructions: https://ubuntu.com/tutorials/how-to-install-ubuntu-on-your-raspberry-pi#1-overview. This uses `rpi-imager` and does not require formatting the SD.
   2. Customize installation (username, wifi etc) and during first boot **pay attention to wait long enough for `cloud-init` to finish ** before login (it stops thinking for a couple of minutes then spits more text), see this note: https://ubuntu.com/tutorials/how-to-install-ubuntu-on-your-raspberry-pi#4-boot-ubuntu-server

   3. update and upgrade

   ```bash
   $ sudo apt update
   $ sudo apt upgrade
   ```

   I also struggled quite a bit with the upgrade, I got a message similar to this one: https://phoenixnap.com/kb/fix-could-not-get-lock-error-ubuntu but linked to `unattended-upgrade`. Finally fixed it after a rather chaotic series of `reboot`, `kill PID` and `sudo rm /var/lib/apt/lists/lock` commands, no idea which one worked.

   4. Then install Mate on top of ubuntu server: https://gcore.com/learning/how-to-install-mate-on-ubuntu/ (see here other ubuntu flavors for pi: https://waldorf.waveform.org.uk/2020/ubuntu-desktops-on-the-pi.html)

   ```bash
   $ sudo apt install ubuntu-mate-desktop
   ```

   When prompted select `lightdm` display manager

   It is veery sloow.

   Reboot

   It works!

   As proposed  [here](https://ubuntu-mate.org/raspberry-pi/) I installed `sshguard` and modified the sound config. I succeeded to get HDMI audio output from HDMI0 (see [here](https://forums.raspberrypi.com/viewtopic.php?t=282220))

## Install needed software 

1. **git** with: `$ sudo apt install git`
2. **arduino**  1.8.19 for ARM with: `$ sudo apt install arduino`. If needed add the user to the `dialout` group with `$ sudo usermod -a -G dialout <username>` and logout (GUI also asks for this, and reminds logout is required). Test with **Blink** from **Examples/01. Basics**
3. **ssh** with: `$ sudo apt install openssh-server` get local IP address of bot with `$ ip addr` and write it down. Now we can remotely ssh from laptop with `ssh <bot_username_bot>@<bot_addr> # e.g. mhered@192.168.8.170`

`$ ssh mhered@sevillabot` didn't work initially because the laptop remembered the old ECDSA fingerprint (before the downgrade from 22.04), so I deleted it with `ssh-keygen -f "/home/mhered/.ssh/known_hosts" -R "192.168.8.170"`

4. **miniterm** with: `$ sudo apt install python3-serial`

5. install and configure vs-code **ssh and arduino extensions** to remotely flash arduino from RPi4 following these instructions: https://www.youtube.com/watch?v=2BJ-iJF04VA:

   * install ssh extension then connect to sevillabot and it installs a vscode server in the Rpi. Then click on arduino extension and it installs remotely in the RPi.

   * In **Extensions Settings** go to the **Remote** tab, **Arduino path**, find the path from terminal with 

     ```
     $ ls -l `which arduino`
     ```

     Then paste the path removing the file name, e.g. `/usr/bin/arduino` > `/usr/bin/`)

- [ ] PENDING Not finished. Need to have arduino files and I am tired today.

## Install ROS Foxy

Follow the official instructions: https://docs.ros.org/en/foxy/Installation/Ubuntu-Install-Debians.html

1. If needed, set locale to support UTF-8
(in minimal environments (e.g. docker), the locale may be something minimal like `POSIX`)

```bash
$ locale  # check for UTF-8
$ sudo apt update && sudo apt install locales
$ sudo locale-gen en_US en_US.UTF-8
$ sudo update-locale LC_ALL=en_US.UTF-8 LANG=en_US.UTF-8
$ export LANG=en_US.UTF-8
$ locale  # verify settings
```

2. Setup Sources

Add the ROS 2 apt repo: 1) ensure [Ubuntu Universe repository](https://help.ubuntu.com/community/Repositories/Ubuntu) is enabled, 2) add the ROS 2 GPG key with apt, and 3) add the repo to your sources list.

``` bash
$ sudo apt install software-properties-common
$ sudo add-apt-repository universe #enable ubuntu universe repo

$ sudo apt update && sudo apt install curl -y
$ sudo curl -sSL https://raw.githubusercontent.com/ros/rosdistro/master/ros.key -o /usr/share/keyrings/ros-archive-keyring.gpg #add gpg key

$ echo "deb [arch=$(dpkg --print-architecture) signed-by=/usr/share/keyrings/ros-archive-keyring.gpg] http://packages.ros.org/ros2/ubuntu $(. /etc/os-release && echo $UBUNTU_CODENAME) main" | sudo tee /etc/apt/sources.list.d/ros2.list > /dev/null # add repo to sources 
```
3. Ensure your system is up to date before installing ROS2 packages. 

```bash
$ sudo apt update && sudo apt upgrade
```
4. Install ROS 2 Desktop Install which includes ROS, RViz, demos, tutorials.

``` bash
$ sudo apt install ros-foxy-desktop python3-argcomplete
```

5. Install dependencies

```bash
$ sudo apt install python3-colcon-common-extensions ros-foxy-ros2-control ros-foxy-xacro ros-foxy-ros2-controllers
```

6. Source the ROS2 environment

```bash
$ echo "source /opt/ros/foxy/setup.bash" >> ~/.bashrc
$ source ~/.bashrc
```

7. Test communication between a C++ node running on the PC and a python node on the bot

```bash
$ ros2 run demo_nodes_py listener
...
[INFO] [1662750392.965285945] [listener]: I heard: [Hello World: 63]
[INFO] [1662750393.965151014] [listener]: I heard: [Hello World: 64]
[INFO] [1662750394.965403701] [listener]: I heard: [Hello World: 65]
...
```

```bash
(PC):$ ros2 run demo_nodes_cpp talker
...
[INFO] [1662750396.990408713] [talker]: Publishing: 'Hello World: 67'
[INFO] [1662750397.990414028] [talker]: Publishing: 'Hello World: 68'
[INFO] [1662750398.990288416] [talker]: Publishing: 'Hello World: 69'
...
```

Hurray! 

Next steps: 

## Create a backup copy of a MicroSD

See: https://www.youtube.com/watch?v=xSxNJSkSgpk. This is critical to keep a clean image for 20.04/foxy and avoid having to repeat this nightmare.

Plug origin and destination microSD in laptop

```bash
$ sudo fdisk -l # display all detected drives, identify origin and destination drives
$ df -h # check there is enough space in destination drive
$ sudo dd bs=4M if=/dev/sdb of=/home/mhered/sevillabot/SD_images/clean_20.04_with_ROS_foxy.img #make image from input drive and save to output file
(Terminal 2):$ watch ls -latrh sevillabot/SD_images/clean*.img #to monitor progress (otherwise output is not verbose). Expect a long time!
$ sudo dd bs=4M if=/home/mhered/sevillabot/SD_images/clean_20.04_with_ROS_foxy.img of=/dev/sdb #save image to destination SD card
```

Open topics:

- [ ] Why do I have a large unallocated partition?
- [ ] Alternative: Try also using a smaller SD card

## Gamepad setup

```bash
$ sudo apt update
$ sudo apt upgrade
$ sudo apt install joystick jstest-gtk evtest
$ sudo apt-get install libcanberra-gtk-module libcanberra-gtk0
```

Initially unable to pair the controller to the headless RPi following these instructions:  https://salamwaddah.com/blog/connecting-ps4-controller-to-raspberry-pi-via-bluetooth. or these instructions https://simpleit.rocks/linux/shell/connect-to-bluetooth-from-cli/

I got a message that no controller was available, and one of the suggested fixes: `systemctl start hciuart`, failed.

Tried several things, not sure which one worked:

* reinstalled packages: `$ sudo apt install --reinstall bluez pi-bluetooth`
* rebooted
* manually started `hciuart` with `$ systemctl start hciuart`
* rebooted again?

And then the pairing worked: 

```bash
$ sudo bluetoothctl
Agent registered
[CHG] Controller D8:3A:DD:64:AA:36 Pairable: yes
[bluetooth]# agent on
Agent is already registered
[bluetooth]# discoverable on
Changing discoverable on succeeded
[CHG] Controller D8:3A:DD:64:AA:36 Discoverable: yes
[bluetooth]# pairable on
Changing pairable on succeeded
[bluetooth]# default-agent
Default agent request successful
[bluetooth]# scan on
Discovery started
...
[NEW] Device A5:15:66:C1:A9:A9 Wireless Controller #when gamepad started pairing
...
[bluetooth]# connect A5:15:66:C1:A9:A9
Attempting to connect to A5:15:66:C1:A9:A9
[CHG] Device A5:15:66:C1:A9:A9 Connected: yes
...
[CHG] Device A5:15:66:C1:A9:A9 UUIDs: 00001124-0000-1000-8000-00805f9b34fb
[CHG] Device A5:15:66:C1:A9:A9 UUIDs: 00001200-0000-1000-8000-00805f9b34fb
[CHG] Device A5:15:66:C1:A9:A9 ServicesResolved: yes
...
[CHG] Device A5:15:66:C1:A9:A9 Paired: yes
Connection successful
...
[Wireless Controller]# trust A5:15:66:C1:A9:A9
[CHG] Device A5:15:66:C1:A9:A9 Trusted: yes
Changing A5:15:66:C1:A9:A9 trust succeeded
...
[Wireless Controller]# quit
```

I can pair the gamepad to the PC and to the RPi using this procedure, it works on PC with `evtest` but not on RPI4.

Actually the blue light is not so blue when connecting to the Pi...

I can survive with the gamepad connected to the PC for the moment, but like to connect to the bot for speed and reliability.

To do:

- [ ] try pairing the gamepad in the GUI (not practical, but useful for troubleshooting purposes)
- [x] Josh recommends wireless with dongle as it is easier to pair than bluetooth... Just ordered it.

## Moving the robot

Continue following instructions here: https://github.com/mhered/manolobot/blob/main/Part-5-Teleoperation-Feb23.md

Create a workspace, clone repos and build

Clone robot repo from sevillabot , diffdrive and serial library from josh fork (using "the good way", making a symlink, see https://github.com/mhered/manolobot/blob/main/Part-4-Simulation-Jan23.md):

```bash
$ git clone https://github.com/mhered/sevillabot.git # clone sevillabot
$ cd ~/git
$ git clone https://github.com/joshnewans/serial_motor_demo.git # clone demo node
$ git clone https://github.com/joshnewans/diffdrive_arduino # clone diffdrive
$ git clone http://github.com/joshnewans/serial # clone serial
$ mkdir -p ~/robot_ws/src # create workspace and make symlinks
$ ln -s ~/sevillabot/sevillabot/ ~/robot_ws/src/ 
$ ln -s ~/git/serial_motor_demo/ ~/robot_ws/src/
$ ln -s ~/git/diffdrive_arduino/ ~/robot_ws/src/ 
$ ln -s ~/git/serial/ ~/robot_ws/src 
```

For demo node, build and source workspace, run the node that listens for commands:

```bash
$ cd ~/robot_ws
$ colcon build --symlink-install
$ source install/setup.bash
$ ros2 run serial_motor_demo driver --ros-args -p serial_port:=/dev/ttyUSB0 -p baud_rate:=57600 -p loop_rate:=30 -p encoder_cpr:=1975
```

In the PC build workspace and run GUI:

```bash
(PC):$ cd dev_ws
(PC):$ source install/setup.bash
(PC):$ $ ros2 run serial_motor_demo gui
```

Hurray! Can control motor over ROS2 with PC and bot in foxy!!

And then, following the instructions in [Quick Start Guide](./Quick-start-guide.md) you can control the robot with a gamepad.

## Camera

1. Connect the Pi camera. Note if camera was connected while the RPi was on, you may need to reboot.

2. Install sfw in Rpi ( **v4l2-utils** video driver library and ros node):

   ```bash
   $ sudo apt update
   $ sudo apt upgrade
   $ sudo apt install libraspberrypi-bin v4l-utils ros-foxy-v4l2-camera
   ```
   
3. If needed add the user to the video group:

   ```bash
   $ sudo usermod -aG video mhered
   ```

   Reboot for group changes to take effect

   ```bash
   $ groups
   mhered adm dialout cdrom sudo audio video plugdev games users input render netdev bluetooth gpio spi i2c
   ```

5. Check the camera is detected and supported with:

```bash
$ vcgencmd get_camera
supported=1 detected=1
```

Initially I got `VCHI initialization failed`. I fixed after adding the line `start_x=1` to file `/boot/firmware/config.txt`, saving and rebooting (solution here: https://askubuntu.com/questions/1211805/raspberry-picamera-on-ubuntu-not-found?rq=1). Well, in actual fact, for 22.04 Josh Newan recommended reinstating the legacy camera driver from 20.04  by editing the following lines in the config file with `(Rpi):$ sudo nano /boot/firmware/config.txt`:

```
...
camera_auto_detect=0 # was 1, modified by MH to reinstate legacy camera driver
display_auto_detect=1
start_x=1 # added by MH to reinstate legacy camera driver
...
```

Check if `v4l` (video for linux) can see the camera with:

```bash
$ v4l2-ctl --list-devices
bcm2835-codec-decode (platform:bcm2835-codec):
	/dev/video10
	/dev/video11
	/dev/video12
	/dev/media1

bcm2835-isp (platform:bcm2835-isp):
	/dev/video13
	/dev/video14
	/dev/video15
	/dev/video16
	/dev/media0

mmal service 16.1 (platform:bcm2835-v4l2):
	/dev/video0
```

Install **image transport library** and **rqt_image_view**:

```bash
$ sudo apt install ros-foxy-image-transport-plugins ros-foxy-rqt-image-view
```

Launch driver node:

```bash
$ ros2 run v4l2_camera v4l2_camera_node --ros-args -p image_size:="[640,480]" -p camera_frame_id:=camera_link_optical
```

Then launch `rqt_image_view` from the PC:

```bash
(PC):$ ros2 run rqt_image_view rqt_image_view
```

Hurray!!  the bot broadcasts video to the laptop.

Note: it broadcasts only over `/image_raw_compressed/`

## Other software and needed config fixes

See https://www.youtube.com/watch?v=qoj5_fVBPII

1. fix screen rotation problem?
2. Setup lidar? ros foxy rplidar

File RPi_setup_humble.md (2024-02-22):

# Raspberry Pi 4B 4Gb setup for ROS2 Humble

Note: I follow these instructions: https://articulatedrobotics.xyz/ready-for-ros-1-what-you-need/ which lead here: https://www.techradar.com/how-to/how-to-install-ubuntu-on-the-raspberry-pi then adapt them following these guidelines to port to Humble: https://www.youtube.com/watch?v=qoj5_fVBPII 

## Install ubuntu MATE 22.04 

ROS2 Humble requires Ubuntu 22.04 Jammy Jellyfish (or derivative)

1. Buy a 64Gb microSD card (as recommended here: https://ubuntu-mate.org/raspberry-pi/).

2. Format the card FAT32. Not straightforward from a Windows 11 computer, which will insist you use exFAT formats for drives >32Gb. Command line: `> format /FS:FAT32 E:` seemed to be working but was veeery slow! Instead I did it in Ubuntu. Straightforward.

3. Download the Ubuntu MATE 22.04.3 LTS arm64 image from here: https://ubuntu-mate.org/download/arm64/jammy/ You may want to verify the checksum (in Windows use`> certutil -hashFile PATH-TO-FILE SHA256`)

4. Flash the image onto the card using e.g. balena etcher. A Windows portable version can be downloaded from here: https://etcher.balena.io/ and run by double-clicking. Flashing was reasonably fast, but verification failed, twice. I tried from linux instead and it worked the first time.

5. Insert the SD card in the RPi, connect it to a keyboard, mouse, screen and power, switch it on, and follow the steps of the ubuntu MATE OS setup process. This takes time. 

6. Set up the network as part of the OS installation. Note I did not use netplan despite [this recommendation](https://articulatedrobotics.xyz/ready-for-ros-2-networking/)

7. Update and upgrade. This fixes some bugs with Welcome, Software Boutique and others, see: https://ubuntu-mate.community/t/ubuntu-mate-welcome-and-software-boutique-fail-to-run-with-similar-errors/25371):
```bash
$ sudo apt update
$ sudo apt upgrade
```
Also it is veery sloow.

At the end of this process some issues remain:
- [ ] still no audio output from RPi HDMI despite I tried several fixes including selecting output, plugging on HDMI0 (from [here](https://forums.raspberrypi.com/viewtopic.php?t=282220)), and modifying config files from [here](https://ubuntu-mate.org/raspberry-pi/).

## Install needed software 

1. **git** with: `$ sudo apt install git`
2. **arduino**  1.8.19 for ARM with: `$ sudo apt install arduino`. Then add the user to the `dialout` group with `$ sudo usermod -a -G dialout <username>` then logout (GUI also asks for this, and reminds logout is required). Serial ports were not working due to a conflict with some Braille package, which needs deinstallling with `$ sudo apt remove brltty` cfr. https://www.youtube.com/watch?v=qoj5_fVBPII. Test with **Blink** and **AnalogReadSerial** from **Examples/01. Basics**
3. **ssh** with: `$ sudo apt install openssh-server` get local IP address of bot with `$ ip addr` and write it down. Now we can remotely ssh from laptop with `ssh <bot_username_bot>@<bot_addr> # e.g. mhered@192.168.8.170`
4. **pyserial-miniterm** (previously `miniterm`, note the change of name in 22.04) with: `$ sudo apt install python3-serial`
5. install and configure vs-code **ssh and arduino extensions** to remotely flash arduino from RPi4 following these instructions: https://www.youtube.com/watch?v=2BJ-iJF04VA

## Install ROS Humble

Follow these instructions: https://docs.ros.org/en/humble/Installation/Ubuntu-Install-Debians.html

1. If needed, set locale to support UTF-8
(in minimal environments (e.g. docker), the locale may be something minimal like `POSIX`)

```bash
$ locale  # check for UTF-8
$ sudo apt update && sudo apt install locales
$ sudo locale-gen en_US en_US.UTF-8
$ sudo update-locale LC_ALL=en_US.UTF-8 LANG=en_US.UTF-8
$ export LANG=en_US.UTF-8
$ locale  # verify settings
```

2. Setup Sources

Add the ROS 2 apt repo: 1) ensure [Ubuntu Universe repository](https://help.ubuntu.com/community/Repositories/Ubuntu) is enabled, 2) add the ROS 2 GPG key with apt, and 3) add the repo to your sources list.

``` bash
$ sudo apt install software-properties-common
$ sudo add-apt-repository universe #enable ubuntu universe repo

$ sudo apt update && sudo apt install curl -y
$ sudo curl -sSL https://raw.githubusercontent.com/ros/rosdistro/master/ros.key -o /usr/share/keyrings/ros-archive-keyring.gpg #add gpg key

$ echo "deb [arch=$(dpkg --print-architecture) signed-by=/usr/share/keyrings/ros-archive-keyring.gpg] http://packages.ros.org/ros2/ubuntu $(. /etc/os-release && echo $UBUNTU_CODENAME) main" | sudo tee /etc/apt/sources.list.d/ros2.list > /dev/null # add repo to sources 
```
3. Ensure your system is up to date before installing ROS2 packages. Always recommended, but particularly in 22.04  `systemd` and `udev`-related packages must be updated before installing ROS 2 or your system may crash.

```bash
$ sudo apt update && sudo apt upgrade
```
4. Install ROS 2 Desktop Install which includes ROS, RViz, demos, tutorials.

``` bash
$ sudo apt install ros-humble-desktop
```

5. Install colcon

```bash
$ sudo apt install python3-colcon-common-extensions
```

5. Source the ROS2 environment

```bash
$ echo "source /opt/ros/humble/setup.bash" >> ~/.bashrc
$ source ~/.bashrc
```

6. Test communication between a C++ node running on the PC and a python node on the bot

```bash
$ ros2 run demo_nodes_py listener
...
[INFO] [1662750392.965285945] [listener]: I heard: [Hello World: 63]
[INFO] [1662750393.965151014] [listener]: I heard: [Hello World: 64]
[INFO] [1662750394.965403701] [listener]: I heard: [Hello World: 65]
...
```

```bash
(PC):$ ros2 run demo_nodes_cpp talker
...
[INFO] [1662750396.990408713] [talker]: Publishing: 'Hello World: 67'
[INFO] [1662750397.990414028] [talker]: Publishing: 'Hello World: 68'
[INFO] [1662750398.990288416] [talker]: Publishing: 'Hello World: 69'
...
```

Hurray! It works even with foxy on PC and humble on RPi!    

Next steps: 

- [ ] upgrade laptop to Humble (see [this Articulated Robotics video](https://www.youtube.com/watch?v=qoj5_fVBPII) and [this Medium article](https://robofoundry.medium.com/notes-on-upgrading-to-ubuntu-22-04-and-ros2-humble-8149804abc91) )
- [ ] or maybe use docker?: https://betterprogramming.pub/how-to-use-docker-to-run-multiple-ros-distributions-on-the-same-machine-d851b42aed5

## Moving the robot

Continue following instructions here: https://www.youtube.com/watch?v=qoj5_fVBPII

Need to install some more dependencies:

```bash
$ sudo apt install ros-humble-ros2-control ros-humble-xacro
```

Create a workspace, clone repos and build

Clone: robot repo from manolobot (used "the good way", making a symlink, see https://github.com/mhered/manolobot/blob/main/Part-4-Simulation-Jan23.md), diffdrive from specific branch of buzzology fork and serial library from josh fork:

```bash
$ git clone https://github.com/mhered/manolobot.git
$ mkdir -p ~/robot_ws/src
$ ln -s ~/manolobot/manolobot_uno/ ~/robot_ws/src/

$ cd ~/robot_ws/src
$ git clone http://github.com/buzzology/diffdrive_arduino
$ cd diffdrive_arduino
$ git checkout 3883c00

$ cd ~/robot_ws/src
$ git clone http://github.com/joshnewans/serial
```

Then build and source workspace, run the node that listens for commands:

```bash
$ cd ~/robot_ws
$ colcon build --symlink-install
$ source install/setup.bash
$ ros2 run serial_motor_demo driver --ros-args -p serial_port:=/dev/ttyUSB0 -p baud_rate:=57600 -p loop_rate:=30 -p encoder_cpr:=1975
```

In the PC build workspace and run GUI:

```bash
(PC):$ cd dev_ws
(PC):$ source install/setup.bash
(PC):$ $ ros2 run serial_motor_demo gui
```

Hurray! Can control motor over ROS2 with PC in foxy and bot in humble!!

However, the original launch file does not work...

```bash
$ ros2 launch manolobot_uno launch_robot.launch.py 
[Some Error]
```

- [ ] To do: find out what is wrong

## Camera

1. Connect the Pi camera. Note if camera was connected while the RPi was on, you may need to reboot.

2. Reinstate the legacy camera driver from 20.04 (fix suggested by Josh Newan) by editing the following lines in the config file with `(Rpi):$ sudo nano /boot/firmware/config.txt`:

   ```
   ...
   camera_auto_detect=0 # was 1, modified by MH to reinstate legacy camera driver
   display_auto_detect=1
   start_x=1 # added by MH to reinstate legacy camera driver
   ...
   ```

3. Install sfw in Rpi ( **v4l2-utils** video driver library and ros node):

   ```bash
   $ sudo apt update
   $ sudo apt upgrade
   $ sudo apt install libraspberrypi-bin v4l-utils ros-humble-v4l2-camera
   ```

4. If needed add the user to the video group:

   ```bash
   $ sudo usermod -aG video mhered
   $ groups
   mhered adm dialout cdrom sudo dip plugdev lpadmin sambashare
   ```

   Reboot for group changes to take effect

5. Check the camera is detected and supported with:

```bash
$ vcgencmd get_camera
supported=1 detected=1, libcamera interfaces=0
```

If the RPi is connected to a screen you may check streaming with:

```bash
$ raspistill -k
```

Quit with `x`

Check if `v4l` (video for linux) can see the camera with:

```bash
$ v4l2-ctl --list-devices
bcm2835-codec-decode (platform:bcm2835-codec):
	/dev/video10
	/dev/video11
	/dev/video12
	/dev/media1

bcm2835-isp (platform:bcm2835-isp):
	/dev/video13
	/dev/video14
	/dev/video15
	/dev/video16
	/dev/media0

mmal service 16.1 (platform:bcm2835-v4l2):
	/dev/video0
```

Install **image transport library** and **rqt_image_view**:

```bash
$ sudo apt install ros-humble-image-transport-plugins ros-humble-rqt-image-view
```

Launch driver node:

```bash
$ ros2 run v4l2_camera v4l2_camera_node --ros-args -p image_size:="[640,480]" -p camera_frame_id:=camera_link_optical
```

Then launch `rqt_image_view` from the PC:

```bash
(PC):$ ros2 run rqt_image_view rqt_image_view
```

Hurray! the bot broadcasts video to the laptop!!

Note: it broadcasts only over `/image_raw_compressed/`

## Other software and needed config fixes

See https://www.youtube.com/watch?v=qoj5_fVBPII

1. fix screen rotation problem?
2. Setup lidar? ros humble rplidar

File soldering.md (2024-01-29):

# Soldering

Soldering tutorial for beginners 5 easy steps: https://www.youtube.com/watch?v=Qps9woUGkvI

Soldering electronics for beginners (Part 1): https://www.youtube.com/watch?v=M2Jf8cebwCs

Soldering crash course: https://www.youtube.com/watch?v=6rmErwU5E-k

## Iron

Recommends temperature controlled station and bevel tips

Maintenance: keep the tip clean with steel wool

## Solder

Usually tin leaded and unleaded. 

Leaded is easier to work with, needs lower temperature (various recommendations 300-400C) but lead is poisonous so wash your hands and have good ventilation e.g. ventilator at your back

## Flux

Stops formation of oxide layer

Two types of Flux: active is corrosive, you need to clean it quickly

Passive: non corrosive (Rosin type). 

Flux comes actually in a channel or core inside the soldering wire

## Soldering wires

Recommends stranded core (easier to handle) and silicon coated (won't melt and easier to strip). 

Tinning the wire: strip off 5mm, twist the strands, then heat the wire with the iron and melt some solder onto it, enough to cover the strands and keep them together

Never melt the solder on the iron then transfer to the part, the flux will get used too early + the part will be cold!

Slide the heat shrink on one end

Move parts together and melt the solder with additional solder

cover with the heat shrink, heat it centre first then ends to avoid trapping air bubbles

## Soldering a pin onto a board

Use the iron to heat the parts (board and pin) then melt the solder on it

Again, never melt the solder on the iron then transfer 

Clean residue of rosin with alcohol

Adding flux will reduce surface tension and make the solder "wet" the surfaces better.

## Soldering a wire onto a pin hole

Prep the hole: heat up then add solder 

strip 2mm, tin the wire

solder

(See details in crash course video)

## Mistakes

never add the solder to the iron

less is more (unless breadboard pins due to mechanical stress and power pins due to high current)

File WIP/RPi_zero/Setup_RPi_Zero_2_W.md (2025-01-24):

# Setup RPi Zero

Followed this tutorial: https://robofoundry.medium.com/running-ros2-foxy-on-raspberry-pi-zero-2w-a4720334d3bb

1. Download [Raspberry Pi Imager for Windows](https://downloads.raspberrypi.org/imager/imager_latest.exe) to write the correct image of Ubuntu 20.04 Focal in a 32Gb SD Card. 
   In the current version there are options to select: 

   * Device: **Raspberry Pi Zero 2 W**
   * OS: **Ubuntu Server 20.04.5 LTS (64-bit)**
   * SD card

   Then you are prompted to apply OS customization settings:

   * in the **General** tab edit hostname, user/pwd, Wifi SSID/pwd, and regional preferences (LAN country, timezone and keyboard)
   * in the **Services** tab activate SSH with password authentication

   With this,there is no need to create/edit ``network-config``. `config.txt` or `bcm2710-rpi-zero-2.dtb` as suggested by the tutorial

2. After burning the image, insert the SD in the Pi Zero, power it up and wait for ~5 minutes to allow for the first boot to complete. If you can connect a monitor wait until text output eventually stops (watch out as there are loong pauses before it finally stops for good). I never got a login prompt, though.
3. Restart the Pi, monitor from the router interface (https://192.168.8.1/ ) until the zero shows up as connected and note the IP address, in my case 192.168.8.182
4. Then ssh into it with: 

```bash
ssh mhered@192.168.8.182
```

5. We can assign a permanent alias to simplify the ssh command to`$ ssh zero` simply adding an entry to `~/.ssh/config` in the PC:

```bash
  Host zero
    HostName 192.168.8.182
    User mhered
```

6. Before running updates, create a swap file - Pi Zero's memory is limited:

```bash
## Please run all commands below without copying $ in front, that's just there to indicate it is a command line and description is in comments starting with ##
## You can check if you have any swap enabled by executing 
free -m
## Create a file:
sudo fallocate -l 1G /var/swapfile
## initialize with zeros (slow)
sudo dd if=/dev/zero of=/var/swapfile bs=1024 count=1048576
## Modify permissions for swapfile
sudo chmod 0600 /var/swapfile
## Create a swap file system on it
sudo mkswap /var/swapfile
## Enable swap
sudo swapon /var/swapfile
## Run following commands to ensure that you indeed have some swap space
free -m
sudo swapon --show
## make it permanent through restarts by adding an entry to /etc/fstab file
sudo nano /etc/fstab
## append following line at the end of /etc/fstab file in nano editor
/var/swapfile swap swap defaults 0 0
## that's it, reboot and make sure to run free -m and sudo swapon --show to make sure the swap file is still maintained after reboot, if it has not, check the entry in /etc/fstab file to make sure it points to exact location of your swap file e.g. /var/swapfile
sudo reboot
```

7. Switch `initramfs` to use ``lz4`` compression - this results in larger output on the boot partition, but is much faster and less memory intensive  iaw Canonical - and update `initramfs`

```bash
## install lz4
sudo apt install lz4
## configure initramfs to use lz4
sudo sed -i -e 's/COMPRESS=zstd/COMPRESS=lz4/' /etc/initramfs-tools/initramfs.conf

## update initramfs boot files (veery slow)
sudo update-initramfs -u

sudo reboot
```

8. update and upgrade (takes a loong time):

```bash
sudo apt update
sudo apt upgrade
```

9. Install ROS2 foxy desktop and dev tools and ROS tools
   Set locale

```bash
locale  # check for UTF-8

sudo apt update && sudo apt install locales
sudo locale-gen en_US en_US.UTF-8 # sloow
sudo update-locale LC_ALL=en_US.UTF-8 LANG=en_US.UTF-8
export LANG=en_US.UTF-8

locale  # verify settings
```

	Set up resources: enable the universe repo, add the ROS2 GPG key and add the repo

```bash
sudo apt install software-properties-common
sudo add-apt-repository universe

sudo apt update && sudo apt install curl -y
sudo curl -sSL https://raw.githubusercontent.com/ros/rosdistro/master/ros.key -o /usr/share/keyrings/ros-archive-keyring.gpg

echo "deb [arch=$(dpkg --print-architecture) signed-by=/usr/share/keyrings/ros-archive-keyring.gpg] http://packages.ros.org/ros2/ubuntu $(. /etc/os-release && echo $UBUNTU_CODENAME) main" | sudo tee /etc/apt/sources.list.d/ros2.list > /dev/null
```

	Install ROS2 desktop (with barebone I could not get the sample nodes to work) and dev tools

```bash
sudo apt update
sudo apt upgrade

sudo apt install ros-foxy-desktop python3-argcomplete

sudo apt install ros-dev-tools
```

Add sourcing to shell startup script:

```bash
echo "source /opt/ros/foxy/setup.bash" >> ~/.bashrc
```

Test ROS2 with basic talker and listener nodes:

```bash
ros2 run demo_nodes_cpp talker
[INFO] [1716508734.685711158] [talker]: Publishing: "Hello World: 0"
[INFO] [1716508735.687527316] [talker]: Publishing: "Hello World: 1"
[INFO] [1716508736.688247732] [talker]: Publishing: "Hello World: 2"
...
```

```bash
ros2 run demo_nodes_py listener
[INFO] [1716508736.689810760] [listener]: I heard: [Hello World: 2]
[INFO] [1716508737.689275068] [listener]: I heard: [Hello World: 3]
[INFO] [1716508738.689336506] [listener]: I heard: [Hello World: 4]
...
```

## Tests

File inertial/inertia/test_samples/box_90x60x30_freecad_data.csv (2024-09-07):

Information of element
________________________
02/09/2024 18:33:18
Document name	Unnamed1
Label of the object	Body
Internal name of the object	Body
Element name
Object Type (Shape)	Solid
Object Type	Part::TopoShape
Mouse coordinates	X	0	mm	Y	0	mm	Z	0	mm
Color on selection
Red	0	Green	0	Blue	0	Transparency	0
Object Color (float) 	Red	0.8	Green	0.8	Blue	0.8	Transparency	0
Object Color (int  ) 	Red	204	Green	204	Blue	204	Transparency	0
Object Color (float) 	Red	0.0980392	Green	0.0980392	Blue	0.0980392	Transparency	0
Color Line(s) (int  ) 	Red	25	Green	25	Blue	25	Transparency	0
Color Point(s) (float) 	Red	0.0980392	Green	0.0980392	Blue	0.0980392	Transparency	0
Color Point(s) (int  ) 	Red	25	Green	25	Blue	25	Transparency	0
Length of the object	0	mm
Shape Perimeter	720	mm
Plane	 XY:	0	 coordinates:	[,0.0 , 0.0,]  [,0.0 , 0.0,]
Plane	 YZ:	0	 coordinates:	[,0.0 , 0.0,]  [,0.0 , 0.0,]
Plane	 ZX:	0	 coordinates:	[,0.0 , 0.0,]  [,0.0 , 0.0,]
Shape area	19800	mm2
Face area	0	mm2
Volume of the form	162000	mm3
Mass	1718.82	g	 Density:	10.61
Shape center	 X:	0	mm	 Y:	0	mm	 Z:	0	mm
Center of mass	 X:	0	mm	 Y:	0	mm	 Z:	0	mm
Overall dimensions	 X:	90	mm	 Y:	60	mm	 Z:	30	mm
Diagonal dimensions	112.25	mm
Direction	 X:	0	 Y:	0	 Z:	30
Matrix of inertia	mm^5
 X:	60750000	 Y:	0	 Z:	0	 :	0
 X:	0	 Y:	121500000	 Z:	0	 :	0
 X:	0	 Y:	0	 Z:	157950000	 :	0
 X:	0	 Y:	0	 Z:	0	 :	1
Matrix inertia massique	gmm2
 X:	644558	 Y:	0	 Z:	0
 X:	0	 Y:	1289115	 Z:	0
 X:	0	 Y:	0	 Z:	1.67585e+06
Matrix Determinant	1.16585e+24
Decimal Determinant	1.16585e+24
Material
Name	Density	Volume	Unit	Price (kg/dm3)	Total cost	Devise	Info
Liquid Water (H2o)	1	162000	mm3	10	17.1882	 Eu	adapt Price
End 	Unnamed1	Body

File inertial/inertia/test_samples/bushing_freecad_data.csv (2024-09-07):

Information of element
________________________
28/08/2024 04:00:27
Document name	Unnamed
Label of the object	Body
Internal name of the object	Body
Element name
Object Type (Shape)	Solid
Object Type	Part::TopoShape
Mouse coordinates	X	0	mm	Y	0	mm	Z	0	mm
Color on selection
Red	0	Green	0	Blue	0	Transparency	0
Object Color (float) 	Red	0.8	Green	0.8	Blue	0.8	Transparency	0
Object Color (int  ) 	Red	204	Green	204	Blue	204	Transparency	0
Object Color (float) 	Red	0.0980392	Green	0.0980392	Blue	0.0980392	Transparency	0
Color Line(s) (int  ) 	Red	25	Green	25	Blue	25	Transparency	0
Color Point(s) (float) 	Red	0.0980392	Green	0.0980392	Blue	0.0980392	Transparency	0
Color Point(s) (int  ) 	Red	25	Green	25	Blue	25	Transparency	0
Length of the object	0	mm
Shape Perimeter	371.327	mm
Plane	 XY:	0	 coordinates:	[,0.0 , 0.0,]  [,0.0 , 0.0,]
Plane	 YZ:	0	 coordinates:	[,0.0 , 0.0,]  [,0.0 , 0.0,]
Plane	 ZX:	0	 coordinates:	[,0.0 , 0.0,]  [,0.0 , 0.0,]
Shape area	8168.14	mm2
Face area	0	mm2
Volume of the form	18849.6	mm3
Mass	199.994	g	 Density:	10.61
Shape center	 X:	0	mm	 Y:	0	mm	 Z:	30	mm
Center of mass	 X:	0	mm	 Y:	0	mm	 Z:	30	mm
Overall dimensions	 X:	25	mm	 Y:	24.9301	mm	 Z:	60	mm
Diagonal dimensions	69.6169	mm
Direction	 X:	0	 Y:	0	 Z:	60
Matrix of inertia	mm^5
 X:	6.65625e+06	 Y:	0	 Z:	0	 :	0
 X:	0	 Y:	6.65625e+06	 Z:	0	 :	0
 X:	0	 Y:	0	 Z:	2.00277e+06	 :	0
 X:	0	 Y:	0	 Z:	0	 :	1
Matrix inertia massique	gmm2
 X:	70622.8	 Y:	0	 Z:	0
 X:	0	 Y:	70622.8	 Z:	0
 X:	0	 Y:	0	 Z:	21249.3
Matrix Determinant	8.87338e+19
Decimal Determinant	8.87338e+19
Material
Name	Density	Volume	Unit	Price (kg/dm3)	Total cost	Devise	Info
Metal Lead (Pb)	11.35	18849.6	mm3	10	1.9999	 Eu	adapt Price
End 	Unnamed	Body
Information of element
________________________
28/08/2024 04:13:37
Document name	Unnamed
Label of the object	Body
Internal name of the object	Body
Element name
Object Type (Shape)	Solid
Object Type	Part::TopoShape
Mouse coordinates	X	0	mm	Y	0	mm	Z	0	mm
Color on selection
Red	0	Green	0	Blue	0	Transparency	0
Object Color (float) 	Red	0.8	Green	0.8	Blue	0.8	Transparency	0
Object Color (int  ) 	Red	204	Green	204	Blue	204	Transparency	0
Object Color (float) 	Red	0.0980392	Green	0.0980392	Blue	0.0980392	Transparency	0
Color Line(s) (int  ) 	Red	25	Green	25	Blue	25	Transparency	0
Color Point(s) (float) 	Red	0.0980392	Green	0.0980392	Blue	0.0980392	Transparency	0
Color Point(s) (int  ) 	Red	25	Green	25	Blue	25	Transparency	0
Length of the object	0	mm
Shape Perimeter	371.327	mm
Plane	 XY:	0	 coordinates:	[,0.0 , 0.0,]  [,0.0 , 0.0,]
Plane	 YZ:	0	 coordinates:	[,0.0 , 0.0,]  [,0.0 , 0.0,]
Plane	 ZX:	0	 coordinates:	[,0.0 , 0.0,]  [,0.0 , 0.0,]
Shape area	8168.14	mm2
Face area	0	mm2
Volume of the form	18849.6	mm3
Mass	18.8496	g	 Density:	1
Shape center	 X:	0	mm	 Y:	0	mm	 Z:	30	mm
Center of mass	 X:	0	mm	 Y:	0	mm	 Z:	30	mm
Overall dimensions	 X:	25	mm	 Y:	24.9301	mm	 Z:	60	mm
Diagonal dimensions	69.6169	mm
Direction	 X:	0	 Y:	0	 Z:	60
Matrix of inertia	mm^5
 X:	6.65625e+06	 Y:	0	 Z:	0	 :	0
 X:	0	 Y:	6.65625e+06	 Z:	0	 :	0
 X:	0	 Y:	0	 Z:	2.00277e+06	 :	0
 X:	0	 Y:	0	 Z:	0	 :	1
Matrix inertia massique	gmm2
 X:	6656.25	 Y:	0	 Z:	0
 X:	0	 Y:	6656.25	 Z:	0
 X:	0	 Y:	0	 Z:	2002.77
Matrix Determinant	8.87338e+19
Decimal Determinant	8.87338e+19
Material
Name	Density	Volume	Unit	Price (kg/dm3)	Total cost	Devise	Info
Liquid Water (H2o)	1	18849.6	mm3	10	0.1885	 Eu	adapt Price
End 	Unnamed	Body
Information of element
________________________
28/08/2024 04:13:39
Document name	Unnamed
Label of the object	Body
Internal name of the object	Body
Element name
Object Type (Shape)	Solid
Object Type	Part::TopoShape
Mouse coordinates	X	0	mm	Y	0	mm	Z	0	mm
Color on selection
Red	0	Green	0	Blue	0	Transparency	0
Object Color (float) 	Red	0.8	Green	0.8	Blue	0.8	Transparency	0
Object Color (int  ) 	Red	204	Green	204	Blue	204	Transparency	0
Object Color (float) 	Red	0.0980392	Green	0.0980392	Blue	0.0980392	Transparency	0
Color Line(s) (int  ) 	Red	25	Green	25	Blue	25	Transparency	0
Color Point(s) (float) 	Red	0.0980392	Green	0.0980392	Blue	0.0980392	Transparency	0
Color Point(s) (int  ) 	Red	25	Green	25	Blue	25	Transparency	0
Length of the object	0	mm
Shape Perimeter	371.327	mm
Plane	 XY:	0	 coordinates:	[,0.0 , 0.0,]  [,0.0 , 0.0,]
Plane	 YZ:	0	 coordinates:	[,0.0 , 0.0,]  [,0.0 , 0.0,]
Plane	 ZX:	0	 coordinates:	[,0.0 , 0.0,]  [,0.0 , 0.0,]
Shape area	8168.14	mm2
Face area	0	mm2
Volume of the form	18849.6	mm3
Mass	18.8496	g	 Density:	1
Shape center	 X:	0	mm	 Y:	0	mm	 Z:	30	mm
Center of mass	 X:	0	mm	 Y:	0	mm	 Z:	30	mm
Overall dimensions	 X:	25	mm	 Y:	24.9301	mm	 Z:	60	mm
Diagonal dimensions	69.6169	mm
Direction	 X:	0	 Y:	0	 Z:	60
Matrix of inertia	mm^5
 X:	6.65625e+06	 Y:	0	 Z:	0	 :	0
 X:	0	 Y:	6.65625e+06	 Z:	0	 :	0
 X:	0	 Y:	0	 Z:	2.00277e+06	 :	0
 X:	0	 Y:	0	 Z:	0	 :	1
Matrix inertia massique	gmm2
 X:	6656.25	 Y:	0	 Z:	0
 X:	0	 Y:	6656.25	 Z:	0
 X:	0	 Y:	0	 Z:	2002.77
Matrix Determinant	8.87338e+19
Decimal Determinant	8.87338e+19
Material
Name	Density	Volume	Unit	Price (kg/dm3)	Total cost	Devise	Info
Liquid Water (H2o)	1	18849.6	mm3	10	0.1885	 Eu	adapt Price
End 	Unnamed	Body
Information of element
________________________
28/08/2024 04:13:41
Document name	Unnamed
Label of the object	Body
Internal name of the object	Body
Element name
Object Type (Shape)	Solid
Object Type	Part::TopoShape
Mouse coordinates	X	0	mm	Y	0	mm	Z	0	mm
Color on selection
Red	0	Green	0	Blue	0	Transparency	0
Object Color (float) 	Red	0.8	Green	0.8	Blue	0.8	Transparency	0
Object Color (int  ) 	Red	204	Green	204	Blue	204	Transparency	0
Object Color (float) 	Red	0.0980392	Green	0.0980392	Blue	0.0980392	Transparency	0
Color Line(s) (int  ) 	Red	25	Green	25	Blue	25	Transparency	0
Color Point(s) (float) 	Red	0.0980392	Green	0.0980392	Blue	0.0980392	Transparency	0
Color Point(s) (int  ) 	Red	25	Green	25	Blue	25	Transparency	0
Length of the object	0	mm
Shape Perimeter	371.327	mm
Plane	 XY:	0	 coordinates:	[,0.0 , 0.0,]  [,0.0 , 0.0,]
Plane	 YZ:	0	 coordinates:	[,0.0 , 0.0,]  [,0.0 , 0.0,]
Plane	 ZX:	0	 coordinates:	[,0.0 , 0.0,]  [,0.0 , 0.0,]
Shape area	8168.14	mm2
Face area	0	mm2
Volume of the form	18849.6	mm3
Mass	18.8496	g	 Density:	1
Shape center	 X:	0	mm	 Y:	0	mm	 Z:	30	mm
Center of mass	 X:	0	mm	 Y:	0	mm	 Z:	30	mm
Overall dimensions	 X:	25	mm	 Y:	24.9301	mm	 Z:	60	mm
Diagonal dimensions	69.6169	mm
Direction	 X:	0	 Y:	0	 Z:	60
Matrix of inertia	mm^5
 X:	6.65625e+06	 Y:	0	 Z:	0	 :	0
 X:	0	 Y:	6.65625e+06	 Z:	0	 :	0
 X:	0	 Y:	0	 Z:	2.00277e+06	 :	0
 X:	0	 Y:	0	 Z:	0	 :	1
Matrix inertia massique	gmm2
 X:	6656.25	 Y:	0	 Z:	0
 X:	0	 Y:	6656.25	 Z:	0
 X:	0	 Y:	0	 Z:	2002.77
Matrix Determinant	8.87338e+19
Decimal Determinant	8.87338e+19
Material
Name	Density	Volume	Unit	Price (kg/dm3)	Total cost	Devise	Info
Liquid Water (H2o)	1	18849.6	mm3	10	0.1885	 Eu	adapt Price
End 	Unnamed	Body
Information of element
________________________
28/08/2024 04:13:41
Document name	Unnamed
Label of the object	Body
Internal name of the object	Body
Element name
Object Type (Shape)	Solid
Object Type	Part::TopoShape
Mouse coordinates	X	0	mm	Y	0	mm	Z	0	mm
Color on selection
Red	0	Green	0	Blue	0	Transparency	0
Object Color (float) 	Red	0.8	Green	0.8	Blue	0.8	Transparency	0
Object Color (int  ) 	Red	204	Green	204	Blue	204	Transparency	0
Object Color (float) 	Red	0.0980392	Green	0.0980392	Blue	0.0980392	Transparency	0
Color Line(s) (int  ) 	Red	25	Green	25	Blue	25	Transparency	0
Color Point(s) (float) 	Red	0.0980392	Green	0.0980392	Blue	0.0980392	Transparency	0
Color Point(s) (int  ) 	Red	25	Green	25	Blue	25	Transparency	0
Length of the object	0	mm
Shape Perimeter	371.327	mm
Plane	 XY:	0	 coordinates:	[,0.0 , 0.0,]  [,0.0 , 0.0,]
Plane	 YZ:	0	 coordinates:	[,0.0 , 0.0,]  [,0.0 , 0.0,]
Plane	 ZX:	0	 coordinates:	[,0.0 , 0.0,]  [,0.0 , 0.0,]
Shape area	8168.14	mm2
Face area	0	mm2
Volume of the form	18849.6	mm3
Mass	18.8496	g	 Density:	1
Shape center	 X:	0	mm	 Y:	0	mm	 Z:	30	mm
Center of mass	 X:	0	mm	 Y:	0	mm	 Z:	30	mm
Overall dimensions	 X:	25	mm	 Y:	24.9301	mm	 Z:	60	mm
Diagonal dimensions	69.6169	mm
Direction	 X:	0	 Y:	0	 Z:	60
Matrix of inertia	mm^5
 X:	6.65625e+06	 Y:	0	 Z:	0	 :	0
 X:	0	 Y:	6.65625e+06	 Z:	0	 :	0
 X:	0	 Y:	0	 Z:	2.00277e+06	 :	0
 X:	0	 Y:	0	 Z:	0	 :	1
Matrix inertia massique	gmm2
 X:	6656.25	 Y:	0	 Z:	0
 X:	0	 Y:	6656.25	 Z:	0
 X:	0	 Y:	0	 Z:	2002.77
Matrix Determinant	8.87338e+19
Decimal Determinant	8.87338e+19
Material
Name	Density	Volume	Unit	Price (kg/dm3)	Total cost	Devise	Info
Liquid Water (H2o)	1	18849.6	mm3	10	0.1885	 Eu	adapt Price
End 	Unnamed	Body
Information of element
________________________
28/08/2024 04:24:53
Document name	Unnamed
Label of the object	Body
Internal name of the object	Body
Element name
Object Type (Shape)	Solid
Object Type	Part::TopoShape
Mouse coordinates	X	0	mm	Y	0	mm	Z	0	mm
Color on selection
Red	0	Green	0	Blue	0	Transparency	0
Object Color (float) 	Red	0.8	Green	0.8	Blue	0.8	Transparency	0
Object Color (int  ) 	Red	204	Green	204	Blue	204	Transparency	0
Object Color (float) 	Red	0.0980392	Green	0.0980392	Blue	0.0980392	Transparency	0
Color Line(s) (int  ) 	Red	25	Green	25	Blue	25	Transparency	0
Color Point(s) (float) 	Red	0.0980392	Green	0.0980392	Blue	0.0980392	Transparency	0
Color Point(s) (int  ) 	Red	25	Green	25	Blue	25	Transparency	0
Length of the object	0	mm
Shape Perimeter	371.327	mm
Plane	 XY:	0	 coordinates:	[,0.0 , 0.0,]  [,0.0 , 0.0,]
Plane	 YZ:	0	 coordinates:	[,0.0 , 0.0,]  [,0.0 , 0.0,]
Plane	 ZX:	0	 coordinates:	[,0.0 , 0.0,]  [,0.0 , 0.0,]
Shape area	8168.14	mm2
Face area	0	mm2
Volume of the form	18849.6	mm3
Mass	199.994	g	 Density:	10.61
Shape center	 X:	0	mm	 Y:	0	mm	 Z:	30	mm
Center of mass	 X:	0	mm	 Y:	0	mm	 Z:	30	mm
Overall dimensions	 X:	25	mm	 Y:	24.9301	mm	 Z:	60	mm
Diagonal dimensions	69.6169	mm
Direction	 X:	0	 Y:	0	 Z:	60
Matrix of inertia	mm^5
 X:	6.65625e+06	 Y:	0	 Z:	0	 :	0
 X:	0	 Y:	6.65625e+06	 Z:	0	 :	0
 X:	0	 Y:	0	 Z:	2.00277e+06	 :	0
 X:	0	 Y:	0	 Z:	0	 :	1
Matrix inertia massique	gmm2
 X:	70622.8	 Y:	0	 Z:	0
 X:	0	 Y:	70622.8	 Z:	0
 X:	0	 Y:	0	 Z:	21249.3
Matrix Determinant	8.87338e+19
Decimal Determinant	8.87338e+19
Material
Name	Density	Volume	Unit	Price (kg/dm3)	Total cost	Devise	Info
Liquid Water (H2o)	1	18849.6	mm3	10	1.9999	 Eu	adapt Price
End 	Unnamed	Body

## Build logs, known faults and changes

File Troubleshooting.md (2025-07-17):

# Troubleshooting

## Issue: bot suddenly stops connecting to host

Happened just at the end of Pi Wars 2024. 

Apparently  for some reason a different IP address was assigned to the Raspberry Pi

To Fix:

1. Connect to RPi with a screen and keyboard, Open a terminal
2. Identify new IP address with:

```bash
$ ip address
...
3: wlan0: 
	...
    inet 192.168.8.179/24 brd ...
...
```

So it is now `192.168.8.179` (it used to be `192.168.8.170`)

4. In the host computer edit `.ssh/config` to replace old IP with new IP

```bash
$ sudo nano .ssh/config
# Read more about SSH config files: https://linux.die.net/man/5/ssh_config
  Host sevillabot
    HostName 192.168.8.179
    User mhered
...
```

5. Try to connect, it will complain that you are renaming a known host, and ask you to remove the old key:

```bash
$ ssh mhered@sevillabot
@@@@@@@@@@@@@@@@@@@@@@@@@@@@@@@@@@@@@@@@@@@@@@@@@@@@@@@@@@@
@    WARNING: REMOTE HOST IDENTIFICATION HAS CHANGED!     @
@@@@@@@@@@@@@@@@@@@@@@@@@@@@@@@@@@@@@@@@@@@@@@@@@@@@@@@@@@@
IT IS POSSIBLE THAT SOMEONE IS DOING SOMETHING NASTY!
Someone could be eavesdropping on you right now (man-in-the-middle attack)!
It is also possible that a host key has just been changed.
The fingerprint for the ECDSA key sent by the remote host is
SHA256:***************************************
Please contact your system administrator.
Add correct host key in /home/mhered/.ssh/known_hosts to get rid of this message.
Offending ECDSA key in /home/mhered/.ssh/known_hosts:6
  remove with:
  ssh-keygen -f "/home/mhered/.ssh/known_hosts" -R "192.168.8.179"
ECDSA host key for 192.168.8.179 has changed and you have requested strict checking.
Host key verification failed.

$ ssh-keygen -f "/home/mhered/.ssh/known_hosts" -R "192.168.8.179"
# Host 192.168.8.179 found: line 6
/home/mhered/.ssh/known_hosts updated.
Original contents retained as /home/mhered/.ssh/known_hosts.old
```

## Scanning for the IP address of `sevillabot`

Easier than connecting the robot to keyboard and screen, assumes MAC address of RPi has not changed (should not unless RPi was replaced or intentionally hacked).

Execute script:

```bash
$ python3 ./commands/find_lost_robot.py
Scanning network for sevillabot...
[sudo] password for mhered: 
✅ Found sevillabot at IP: 192.168.8.179
```

Note `arp` is a dependency of this python script, may need to install it with:

```bash
$ sudo apt install arp-scan
```

## Checking IP addres of robot

Another way is to go to the router:
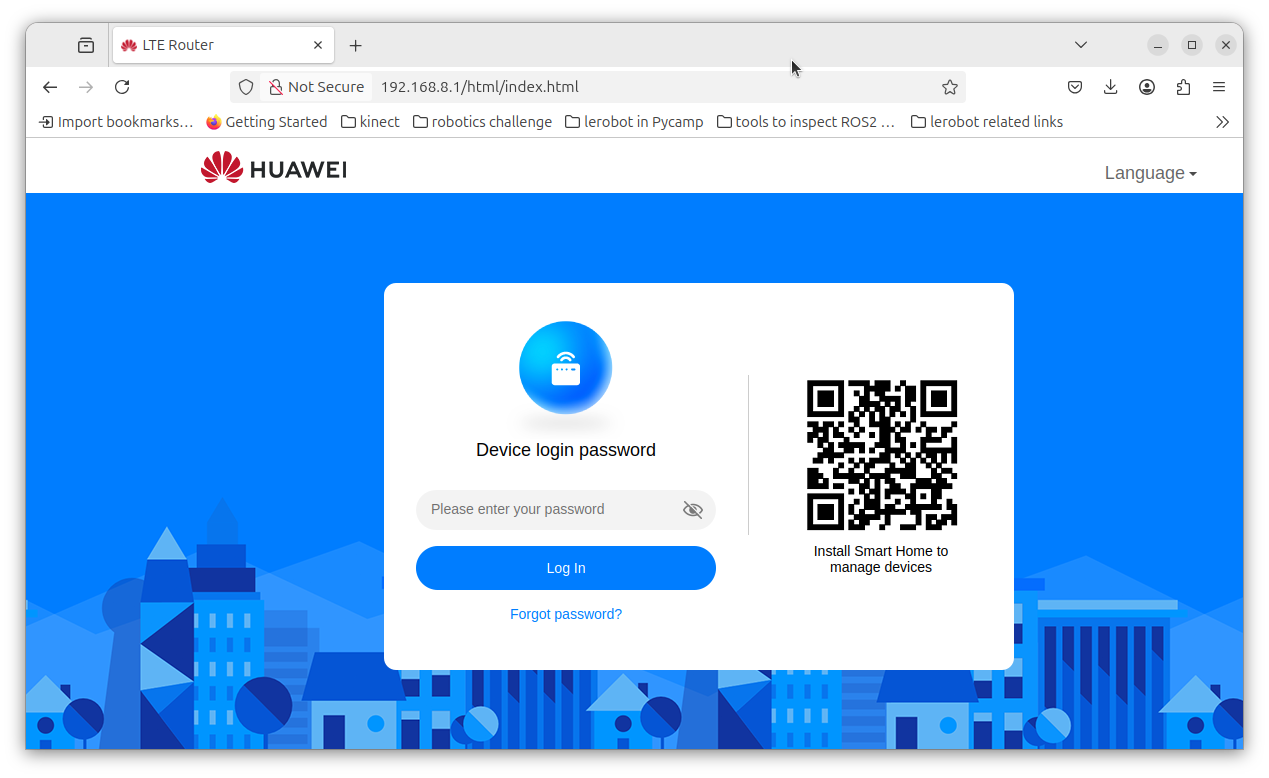
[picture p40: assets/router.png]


Go to **Devices** and search for the robot by name or MAC, note down its IP address.

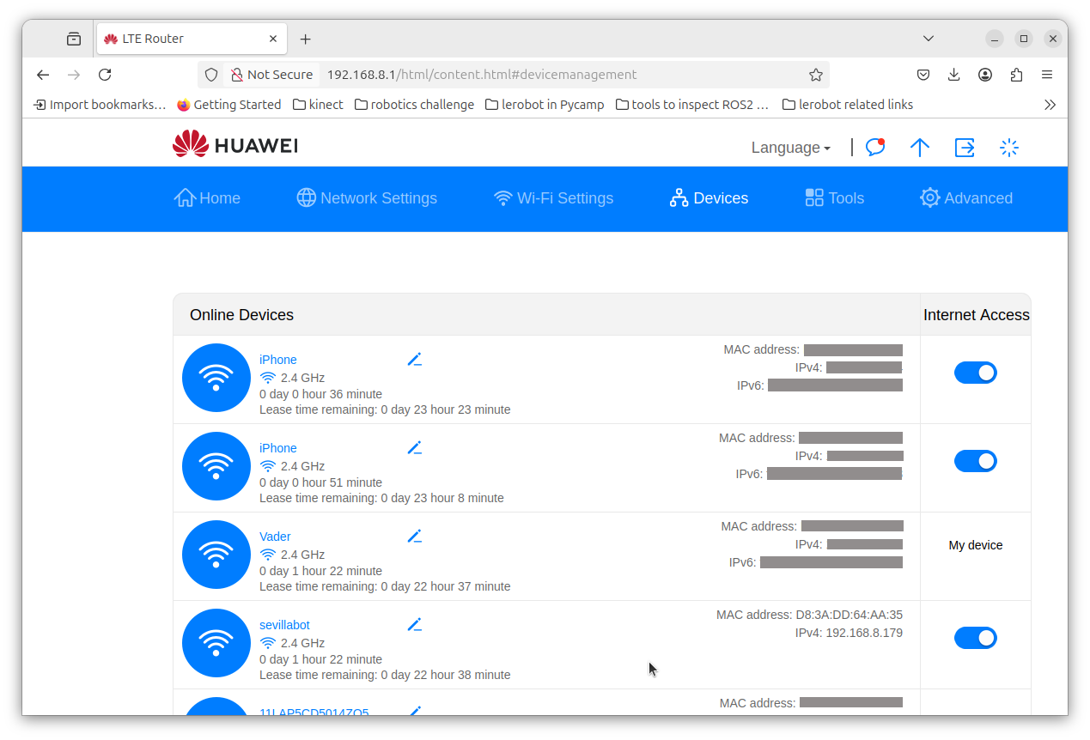
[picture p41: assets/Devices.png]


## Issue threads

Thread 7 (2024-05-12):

fine tune line follower

mhered, 2024-05-12:
* [Pololu - QTR-8RC Reflectance Sensor Array](https://www.pololu.com/product/961/resources)
* [Pololu - 7. Additional Considerations](https://www.pololu.com/docs/0J12/7)

* [tutorial line follower qtr-8rc - Google Search](https://www.google.com/search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,vid:dc7miznXZdI,st:0)
* [Line Follower Robot : Arduino NANO - QTR-8RC - PID Line Follower Robot V1 - Arnab Kumar Das](https://www.arnabkumardas.com/line-follower-robot/arduino-nano-qtr-8rc-line-follower-robot-v1/)
* [Contact - Arnab Kumar Das - Projects - Tutorials - DIY Guides](https://www.arnabkumardas.com/contact/)
* [tutorial line follower robot qtr-8rc - Google Search](https://www.google.com/search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,vid:8JttHLi3sAc,st:0)
* [(4) I made a SUPER FAST Line Follower Robot Using PID! - YouTube](https://www.youtube.com/watch?v=QoNkpnpvEqc)
* [Black and white line following - Support / Robots - Pololu Forum](https://forum.pololu.com/t/black-and-white-line-following/1902)
* [(4) How to code your Line follower robot with PID control and working code! - YouTube](https://www.youtube.com/watch?v=8Lj5ycrT9Fw)
* [PID Based Line Following Robot With POLOLU QTR 8RC-sensor Array : 6 Steps (with Pictures) - Instructables](https://www.instructables.com/PID-Based-Line-Following-Robot-With-POLALU-QTR-8RC/)
* [Stuck with line follower robot project (Pololu QTR 8rc) - Robotics and electronics discussion / Electronics - Pololu Forum](https://forum.pololu.com/t/stuck-with-line-follower-robot-project-pololu-qtr-8rc/22104)
* [(4) Arduino Nano PID Line Follower Robot 🤖 - YouTube](https://www.youtube.com/watch?v=7-ju19RMWlw)
* [(4) Controlling Self Driving Cars - YouTube](https://www.youtube.com/watch?v=4Y7zG48uHRo)
* [(4) How to Write a Simple PID Line Follow Algorithm - YouTube](https://www.youtube.com/watch?v=PP4fvBVe3rI)
* [gabrielnhn/ros2-line-follower: A ROS2 package designed to have a differential drive robot follow a Robotrace track by using a camera.](https://github.com/gabrielnhn/ros2-line-follower)
* [File not found](https://github.com/gabrielnhn/ros2-line-follower/blob/main/docs/warnings.md)
* [Home - Arnab Kumar Das - Projects - Tutorials - DIY Guides](https://www.arnabkumardas.com/)
* [Pololu - QTR-8RC Reflectance Sensor Array](https://www.pololu.com/product/961)
* [Pololu - 5.g. Pololu3pi - Sensor Library for the 3pi Robot](https://www.pololu.com/docs/0J17/5.g)
* [Pololu - 3.k. Pololu QTR Sensor Functions](https://www.pololu.com/docs/0J20/3.k)
* [GitHub - pololu/qtr-sensors-arduino: Arduino library for the Pololu QTR reflectance sensors](https://github.com/pololu/qtr-sensors-arduino)
* [Pololu - 5. Related resources](https://www.pololu.com/docs/0J13/5)
* [PID Line Follower Tuning KP=0.038 KD=2.76 - YouTube](https://www.youtube.com/watch?v=VTryE4LCvic&list=PLqr8J8t_ccS1NoCiS0duD3JlDJAMtGg48)

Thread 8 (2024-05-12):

fix limit switches in clamp

mhered, 2024-05-12:
I noticed during piwars 2024 that limit switches were not working.
I am sure it had worked at some point though...
Troubleshoot and fix

References:
[How to implement a limit switch for a stepper motor? - Using Arduino / Programming Questions - Arduino Forum](https://forum.arduino.cc/t/how-to-implement-a-limit-switch-for-a-stepper-motor/1080932/18)
            [(25) Stepper motor with Limit switch Arduino basic usage - YouTube](https://www.youtube.com/watch?v=3SM9Cq7TtMo&t=7s)
            [Arduino/stepper_with_limit_test_1/stepper_with_limit_test_1.ino at master · jumejume1/Arduino](https://github.com/jumejume1/Arduino/blob/master/stepper_with_limit_test_1/stepper_with_limit_test_1.ino)
            [Motor with 2 limit switches - Using Arduino / Programming Questions - Arduino Forum](https://forum.arduino.cc/t/motor-with-2-limit-switches/1111641/6)
            [(4) Wiring Limit Switches Arduino Tutorial - YouTube](https://www.youtube.com/watch?v=6wuInF9Yw08)

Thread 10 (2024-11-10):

Add IMU and sensor fusion

mhered, 2024-11-10:
TO DO
- follow lessons on bumperbot course
- create driver code for sevillabot, ref. also https://github.com/hiwad-aziz/ros2_mpu6050_driver and https://www.youtube.com/watch?v=TaHY4OYBNwc-
- make  3d printed part and install IMU
- create sensor fusion code, ref. also https://www.youtube.com/watch?v=OopVfPZ2_ig
- test

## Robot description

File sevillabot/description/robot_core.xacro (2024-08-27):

<?xml version="1.0"?>
<robot xmlns:xacro="http://www.ros.org/wiki/xacro">

    <!-- MATERIALS -->
    <!-- white black light_gray dark_gray green blue red yellow orange -->

    <xacro:include filename="materials.xacro" />

    <!-- INERTIAL MACROS -->

    <xacro:include filename="inertial_macros.xacro" />

    <!-- BASE LINK -->

    <link name="base_link">
    </link>length

    <!-- BASE_FOOTPRINT LINK -->
    
    <joint name="base_footprint_joint" type="fixed">
        <parent link="base_link" />
        <child link="base_footprint" />
        <origin xyz="0 0 0" rpy="0 0 0" />
    </joint>

    <link name="base_footprint">
    </link>

    <!-- CHASSIS LINK -->

    <joint name="chassis_joint" type="fixed">
        <parent link="base_link" />
        <child link="chassis_link" />
        <origin xyz="0 0 0" />
    </joint>

    <link name="chassis_link">
        <visual>
            <geometry>
            	<mesh filename="file://$(find sevillabot)/meshes/ASSY_sevillabot_base.stl" scale="1.0e-3 1.0e-3 1.0e-3"/>
            </geometry>
            <origin xyz="${box_z_off} 0 ${box_z_off}" rpy="0 0 0"/>
            <material name="white" />
        </visual>

        <collision>
            <geometry>
                <box size="${box_x} ${box_y} ${box_z}" />
            </geometry>
            <origin xyz="0 0 ${box_z/2}" />
        </collision>

        <xacro:inertial_box mass="${box_mass}" x="${box_x}" y="${box_y}" z="${box_z}">
            <origin xyz="0 0 0" rpy="0 0 0" />
        </xacro:inertial_box>

    </link>

    <gazebo reference="chassis_link">
        <material>Gazebo/White</material>
    </gazebo>

    <!-- LEFT WHEEL LINK -->

    <joint name="left_wheel_joint" type="continuous">
        <parent link="base_link" />
        <child link="left_wheel_link" />
        <origin xyz="-${W_x} ${W_y} -${W_z}" rpy="0 0 ${pi/2}" />
        <axis xyz="1 0 0" />
    </joint>

    <link name="left_wheel_link">
        <visual>
            <geometry>
                <mesh filename="file://$(find sevillabot)/meshes/ASSY_Wheel.stl" scale="1.0e-3 1.0e-3 1.0e-3"/>
            </geometry>
            <material name="blue" />
        </visual>

        <collision>
            <geometry>
                <sphere radius="${W_D/2}" />
            </geometry>
        </collision>

        <xacro:inertial_cylinder mass="${W_mass}" radius="${W_D/2}" length="${W_h}">
            <origin xyz="0 0 0" rpy="${pi/2} 0 ${pi/2}" />
        </xacro:inertial_cylinder>

    </link>

    <gazebo reference="left_wheel_link">
        <material>Gazebo/Blue</material>
    </gazebo>

    <!-- RIGHT WHEEL LINK -->

    <joint name="right_wheel_joint" type="continuous">
        <parent link="base_link" />
        <child link="right_wheel_link" />
        <origin xyz="-${W_x} -${W_y} -${W_z}" rpy="0 0 -${pi/2}" />
        <axis xyz="-1 0 0" />
    </joint>

    <link name="right_wheel_link">
        <visual>
            <geometry>
                <!-- cylinder radius="${W_D/2}" length="${W_h}" / -->
                <mesh filename="file://$(find sevillabot)/meshes/ASSY_Wheel.stl" scale="1.0e-3 1.0e-3 1.0e-3"/>
            </geometry>
            <material name="blue" />
        </visual>

        <collision>
            <geometry>
                <sphere radius="${W_D/2}" />
            </geometry>
        </collision>

        <xacro:inertial_cylinder mass="${W_mass}" radius="${W_D/2}" length="${W_h}">
            <origin xyz="0 0 0" rpy="${pi/2} 0 ${pi/2}" />
        </xacro:inertial_cylinder>

    </link>

    <gazebo reference="right_wheel_link">
        <material>Gazebo/Blue</material>
    </gazebo>

    <!-- CASTER WHEEL LINK -->

    <joint name="caster_wheel_joint" type="fixed">
        <parent link="chassis_link" />
        <child link="caster_wheel_link" />
        <origin xyz="${c_x_off} 0 ${-c_z_off}" rpy = "0 0 0" />
    </joint>

    <link name="caster_wheel_link">
        <visual>
            <geometry>
                <!-- sphere radius="${c_D/2}" / -->
                <mesh filename="file://$(find sevillabot)/meshes/ADDON_caster_wheel.stl" scale="1.0e-3 1.0e-3 1.0e-3"/>
            </geometry>
            <origin xyz="0 0 0" rpy = "0 0 0" />
            <material name="yellow" />
        </visual>

        <collision>
            <origin xyz="0 0 0" rpy="0 0 0" />
            <geometry>
                <sphere radius="${c_D/2}" />
            </geometry>
        </collision>

        <xacro:inertial_sphere mass="${c_mass}" radius="${c_D/2}">
            <origin xyz="0 0 0" rpy="0 0 0" />
        </xacro:inertial_sphere>

    </link>

    <gazebo reference="caster_wheel_link">
        <material>Gazebo/Yellow</material>
        <mu1 value="0.0001" />
        <mu2 value="0.0001" />
    </gazebo>


</robot>

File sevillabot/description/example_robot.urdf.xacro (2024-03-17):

<?xml version="1.0"?>
<robot xmlns:xacro="http://www.ros.org/wiki/xacro" name="robot">

    <material name="grey">
        <color rgba="0.2 0.2 0.2 1"/>
    </material>

    <material name="white">
        <color rgba="1 1 1 1"/>
    </material>

    <material name="orange">
        <color rgba="1 0.3 0.1 1"/>
    </material>

    <material name="blue">
        <color rgba="0 0 1 1"/>
    </material>


    <link name="world"></link>

    <joint name="world_to_base" type="fixed">
        <parent link="world" />
        <child link="base" />
        <origin rpy="1.57 0 0" xyz="0 0 0" />
    </joint>

    <link name="base">
        <visual>
            <origin xyz="2 0 0" rpy="0 0 0"/>
            <geometry>
                <box size="5 0.1 3" />
            </geometry>
            <material name="grey" />
        </visual>
    </link>


    <joint name="base_to_l3" type="revolute">
        <parent link="base" />
        <child link="l3" />
        <origin rpy="0 0 0" xyz="0 0.25 0" />
        <axis rpy="0 0 0" xyz="0 0 1" />
        <limit effort="0.1" lower="-3.1" upper="3.1" velocity="0.2"/>
    </joint>


    <link name="l3">
        <visual>
            <origin xyz="0.75 0 0" rpy="0 1.57 0"/>
            <geometry>
                <cylinder length="1.5" radius="0.04" />
            </geometry>
            <material name="orange" />
        </visual>
    </link>

    <joint name="l3_to_l2" type="revolute">
        <parent link="l3" />
        <child link="l2" />
        <!-- <origin xyz="1 0 0" /> -->
        <origin rpy="0 0 0" xyz="1.5 0 0" />
        <axis rpy="0 0 0" xyz="0 0 1" />
        <limit effort="0.1" lower="-3.1" upper="3.1" velocity="0.2"/>
    </joint>


    <link name="l2">
        <visual>
            <origin xyz="0.75 0 0" rpy="0 1.57 0"/>
            <geometry>
                
                <cylinder length="1.5" radius="0.04" />
            </geometry>
            <material name="orange" />
        </visual>
    </link>

    <joint name="l2_to_l1" type="revolute">
        <parent link="l2" />
        <child link="l1" />
        <origin rpy="0 0 0" xyz="1.5 0 0" />
        <axis rpy="0 0 0" xyz="0 0 1" />
        <limit effort="0.1" lower="-3.1" upper="3.1" velocity="0.2"/>
    </joint>


    <link name="l1">
        <visual>
            <origin xyz="0.5 0 0" rpy="0 1.57 0"/>
            <geometry>
                
                <cylinder length="1" radius="0.04" />
            </geometry>
            <material name="orange" />
        </visual>
    </link>


    <joint name="l1_to_grip" type="revolute">
        <parent link="l1" />
        <child link="grip" />
        <origin rpy="0 0 0" xyz="1 0 0" />
        <axis rpy="0 0 0" xyz="0 0 1" />
        <limit effort="0.1" lower="-3.1" upper="3.1" velocity="0.2"/>
    </joint>


    <link name="grip">
        <visual>
            <origin xyz="0.25 0 0"/>
            <geometry>
                <box size="0.5 0.5 0.05" />
            </geometry>
            <material name="white" />
        </visual>
    </link>



    <joint name="world_to_camera" type="fixed">
        <parent link="world" />
        <child link="camera" />
        <origin rpy="-2 0 2.5" xyz="4 1 2" />
    </joint>

    <link name="camera">
        <visual>
            <origin xyz="0 0 -0.2"/>
            <geometry>
                <box size="0.2 0.2 0.4" />
            </geometry>
            <material name="blue" />
        </visual>
    </link>


</robot>

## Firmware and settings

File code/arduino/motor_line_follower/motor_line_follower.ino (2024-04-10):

// Motor A connections
int enA = 9;
int in1 = 8;
int in2 = 7;

// Motor B connections
int enB = 3;
int in3 = 5;
int in4 = 4;

// Line follower connections
const int pinRotate = A0;
const int RotateMin = 0;
const int RotateMax = 1023;
const int pinSpeed = A1;
const int SpeedMin = 0;
const int SpeedMax = 1023;


void setup() {

  Serial.begin(9600);
  // Set all the motor control pins to outputs
  pinMode(enA, OUTPUT);
  pinMode(enB, OUTPUT);
  pinMode(in1, OUTPUT);
  pinMode(in2, OUTPUT);
  pinMode(in3, OUTPUT);
  pinMode(in4, OUTPUT);

  // Turn off motors - Initial state
  digitalWrite(in1, LOW);
  digitalWrite(in2, LOW);
  digitalWrite(in3, LOW);
  digitalWrite(in4, LOW);
}

void loop() {

  //read values
  int RotateValue = getRotateValue();
  int SpeedValue = getSpeedValue();

  //compute motorA, motorB and fwdA, fwdB from input RotateValue, SpeedValue
  bool fwdA = true;
  bool fwdB = true;
  int motorA = map(SpeedValue, SpeedMin, SpeedMax, 255, -255) +
               map(RotateValue, RotateMin, RotateMax, -255, 255);
  int motorB = map(SpeedValue, SpeedMin, SpeedMax, 255, -255) -
               map(RotateValue, RotateMin, RotateMax, -255, 255);

  if (motorA < 0)
  {
    fwdA = false;
    motorA = - motorA;
  }

  if (motorB < 0)
  {
    fwdB = false;
    motorB = - motorB;
  }

  if (motorA > 255) motorA = 255;
  if (motorB > 255) motorB = 255;

  // avoid humming
  if (motorA < 15) motorA = 0;
  if (motorB < 15) motorB = 0;


  showValuesSerial(RotateValue, SpeedValue, motorA, fwdA, motorB, fwdB);

  operateMotors(motorA, fwdA, motorB, fwdB, in1, in2, in3, in4, enA, enB);

  if (fwdA == true)
  {
    // move motor A forward
    digitalWrite(in1, HIGH);
    digitalWrite(in2, LOW);
  }
  else {
    // move motor A in reverse
    digitalWrite(in1, LOW);
    digitalWrite(in2, HIGH);
  }

  if (fwdB == true)
  {
    // move motor B forward
    digitalWrite(in3, HIGH);
    digitalWrite(in4, LOW);
  }
  else {
    // move motor B in reverse
    digitalWrite(in3, LOW);
    digitalWrite(in4, HIGH);
  }

  analogWrite(enA, motorA);
  analogWrite(enB, motorB);

  delay(100);
}

int getRotateValue()
{

  int result = 0;
  delay(100);   // short delay needed between analog readings
  result = analogRead(pinRotate);
  return result;
}

int getSpeedValue()
{
  int result = 0;
  delay(100);   // short delay needed between analog readings
  result = analogRead(pinSpeed);
  return result;
}

void showValuesSerial(int RotateValue, int SpeedValue,
                      int motorA, bool fwdA,
                      int motorB, bool fwdB)
{
  Serial.print("(X, Y): (");
  Serial.print(RotateValue);
  Serial.print(", ");
  Serial.print(SpeedValue);
  Serial.print(") | motorA: ");
  if (fwdA == false) {
    Serial.print("-");
  }
  Serial.print(map(motorA, 0, 255, 0, 100));
  Serial.print("% | motorB: ");
  if (fwdB == false) {
    Serial.print("-");
  }
  Serial.print(map(motorB, 0, 255, 0, 100));
  Serial.println("%");
}

void operateMotors(int motorA, bool fwdA, int motorB, bool fwdB,
                   int in1, int in2, int in3, int in4, int enA, int enB)
{

  if (fwdA == true)
  {
    // move motor A forward
    digitalWrite(in1, HIGH);
    digitalWrite(in2, LOW);
  }
  else {
    // move motor A in reverse
    digitalWrite(in1, LOW);
    digitalWrite(in2, HIGH);
  }

  if (fwdB == true)
  {
    // move motor B forward
    digitalWrite(in3, HIGH);
    digitalWrite(in4, LOW);
  }
  else {
    // move motor B in reverse
    digitalWrite(in3, LOW);
    digitalWrite(in4, HIGH);
  }

  analogWrite(enA, motorA);
  analogWrite(enB, motorB);

}

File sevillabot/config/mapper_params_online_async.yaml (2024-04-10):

slam_toolbox:
  ros__parameters:

    # Plugin params
    solver_plugin: solver_plugins::CeresSolver
    ceres_linear_solver: SPARSE_NORMAL_CHOLESKY
    ceres_preconditioner: SCHUR_JACOBI
    ceres_trust_strategy: LEVENBERG_MARQUARDT
    ceres_dogleg_type: TRADITIONAL_DOGLEG
    ceres_loss_function: None

    # ROS Parameters
    odom_frame: odom
    map_frame: map
    base_frame: base_footprint
    scan_topic: /scan
    mode: localization # localization or mapping depending on the activity

    # if you'd like to immediately start continuing a map at a given pose
    # or at the dock, but they are mutually exclusive, if pose is given
    # will use pose
    map_file_name: /home/mhered/sevillabot/sevillabot/maps/map_obstacles_serial
    # map_start_pose: [0.0, 0.0, 0.0]
    map_start_at_dock: true

    debug_logging: false
    throttle_scans: 1
    transform_publish_period: 0.02 #if 0 never publishes odometry
    map_update_interval: 5.0
    resolution: 0.05
    max_laser_range: 20.0 #for rastering images
    minimum_time_interval: 0.5
    transform_timeout: 0.2
    tf_buffer_duration: 30.
    stack_size_to_use: 40000000 #// program needs a larger stack size to serialize large maps
    enable_interactive_mode: true

    # General Parameters
    use_scan_matching: true
    use_scan_barycenter: true
    minimum_travel_distance: 0.5
    minimum_travel_heading: 0.5
    scan_buffer_size: 10
    scan_buffer_maximum_scan_distance: 10.0
    link_match_minimum_response_fine: 0.1  
    link_scan_maximum_distance: 1.5
    loop_search_maximum_distance: 3.0
    do_loop_closing: true 
    loop_match_minimum_chain_size: 10           
    loop_match_maximum_variance_coarse: 3.0  
    loop_match_minimum_response_coarse: 0.35    
    loop_match_minimum_response_fine: 0.45

    # Correlation Parameters - Correlation Parameters
    correlation_search_space_dimension: 0.5
    correlation_search_space_resolution: 0.01
    correlation_search_space_smear_deviation: 0.1 

    # Correlation Parameters - Loop Closure Parameters
    loop_search_space_dimension: 8.0
    loop_search_space_resolution: 0.05
    loop_search_space_smear_deviation: 0.03

    # Scan Matcher Parameters
    distance_variance_penalty: 0.5      
    angle_variance_penalty: 1.0    

    fine_search_angle_offset: 0.00349     
    coarse_search_angle_offset: 0.349   
    coarse_angle_resolution: 0.0349        
    minimum_angle_penalty: 0.9
    minimum_distance_penalty: 0.5
    use_response_expansion: true

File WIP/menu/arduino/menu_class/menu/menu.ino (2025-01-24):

// 128x64 OLED Display menu controlled by a KY-40 encoder
// mhered 2024
// Vaguely inspired in three different tutorials by: 
// - upir (Menu design): https://youtu.be/HVHVkKt-ldc 
// - LaBuhardillaDelLoco (Adafruit GPX library for OLED): https://youtu.be/cWgWvNhWg-A 
// - Yvan  (Encoder input): https://www.brainy-bits.com/post/best-code-to-use-with-a-ky-040-rotary-encoder-let-s-find-out// see https://wokwi.com/projects/397015999090347009

#include "src/Encoder.h" // custom Encoder library

#include <Adafruit_GFX.h> // graphical library
#include <Adafruit_SSD1306.h> // SSD1306 controller library

// Custom fonts
#include <Fonts/FreeSans9pt7b.h>
#include <Fonts/FreeSansBold9pt7b.h>

// OLED display constants
#define SCREEN_ADDRESS 0x3C // alternatively try 0x3D
#define SCREEN_WIDTH  128 // OLED display width, in pixels
#define SCREEN_HEIGHT 64 // OLED display height, in pixels
#define OLED_RESET    -1 // Reset pin # if screen has 5th wire (or -1 otherwise)

// Declaration for an Encoder
// define pins
#define CLK_PIN 2 
#define DT_PIN  4
#define SW_PIN  3

// create instance of Encoder
Encoder menuEncoder(CLK_PIN, DT_PIN, SW_PIN); // Create an Encoder object for pins provided

// Declaration for an SSD1306 display connected to I2C (SDA, SCL pins)
// The pins for I2C are defined by the Wire-library.
// For arduino UNO or NANO:       A4(SDA), A5(SCL)

// create instance of OLED display
Adafruit_SSD1306 display(SCREEN_WIDTH,
                         SCREEN_HEIGHT,
                         &Wire,
                         OLED_RESET); // &Wire is pointer to I2C comms




// definition to avoid magic numbers
const int MENU_SCREEN = 0;
const int OPTION_SCREEN = 1;

const int NUM_ITEMS = 6; // number of items in the list
const int MAX_ITEM_LENGTH = 20; // maximum characters for the item name

char menu_items [NUM_ITEMS] [MAX_ITEM_LENGTH] = {  // array with item names
  { "1.Toxic" },
  { "2.Zombies" },
  { "3.Tracker" },
  { "4.Mines" },
  { "5.Navigator" },
  { "6.Maze" }
};

int item_selected = 0; // which item in the menu is selected

int current_screen = MENU_SCREEN;

// for 50Hz refresh rate -> refreshDelay = 20
long lastRefreshTime = 0;
int refreshDelay = 200;


// arrays below were generated from B/W images using image2cpp online tool
// ------------------ generated bitmaps from image2cpp ---------------------------------

// 'icon01', 14x14px
const unsigned char bitmap_icon01 [] PROGMEM = {
  0x40, 0x08, 0xc0, 0x1c, 0x60, 0x30, 0x37, 0xa0, 0x1f, 0xc0, 0x27, 0x20, 0x62, 0x30, 0x72, 0x70,
  0x3f, 0xe0, 0x0a, 0x80, 0x2f, 0xa0, 0x69, 0xd8, 0xcc, 0xcc, 0x47, 0x88
};
// 'icon02', 14x14px
const unsigned char bitmap_icon02 [] PROGMEM = {
  0x02, 0x00, 0x0f, 0x80, 0x12, 0x40, 0x22, 0x20, 0x40, 0x10, 0x40, 0x10, 0xf2, 0x78, 0x40, 0x10,
  0x40, 0x10, 0x22, 0x20, 0x12, 0x40, 0x0f, 0x80, 0x02, 0x00, 0x00, 0x00
};
// 'icon03', 14x14px
const unsigned char bitmap_icon03 [] PROGMEM = {
  0x00, 0x38, 0x00, 0x7c, 0x00, 0x6c, 0x00, 0x38, 0x00, 0x38, 0x00, 0x10, 0x06, 0xc0, 0x18, 0x00,
  0x60, 0x00, 0x3c, 0x00, 0x07, 0xc0, 0x00, 0xf8, 0x00, 0x3c, 0x00, 0x7c
};
// 'icon04', 14x14px
const unsigned char bitmap_icon04 [] PROGMEM = {
  0x01, 0x00, 0x01, 0x00, 0x21, 0x08, 0x13, 0x90, 0x0f, 0xe0, 0x09, 0xe0, 0x11, 0xf0, 0xf3, 0xfc,
  0x1f, 0xf0, 0x0f, 0xe0, 0x0f, 0xe0, 0x13, 0x90, 0x21, 0x08, 0x01, 0x00
};
// 'icon05', 14x14px
const unsigned char bitmap_icon05 [] PROGMEM = {
  0x0f, 0x80, 0x10, 0x40, 0x22, 0x20, 0x42, 0x10, 0x80, 0x88, 0x83, 0x0c, 0xb5, 0x6c, 0x86, 0x0c,
  0x88, 0x0c, 0x42, 0x1c, 0x22, 0x38, 0x10, 0x70, 0x0f, 0xe0, 0x07, 0xc0
};
// 'icon06', 14x14px
const unsigned char bitmap_icon06 [] PROGMEM = {
  0xff, 0xfc, 0xb0, 0x44, 0x87, 0x10, 0xfd, 0x7c, 0x81, 0x04, 0xbf, 0x7c, 0x80, 0x04, 0xf7, 0xf4,
  0x80, 0x04, 0xbf, 0xfc, 0x80, 0x04, 0xfb, 0xf4, 0x82, 0x04, 0xfe, 0xfc
};

// Array of all bitmaps for convenience.
const unsigned char* bitmap_icons[NUM_ITEMS] = {
  bitmap_icon01,
  bitmap_icon02,
  bitmap_icon03,
  bitmap_icon04,
  bitmap_icon05,
  bitmap_icon06
};

// 'scrollbar_background', 8x48px
const unsigned char bitmap_scrollbar_background [] PROGMEM = {
  0x00, 0x10, 0x00, 0x10, 0x00, 0x10, 0x00, 0x10, 0x00, 0x10, 0x00, 0x10, 0x00, 0x10, 0x00, 0x10, 
  0x00, 0x10, 0x00, 0x10, 0x00, 0x10, 0x00, 0x10, 0x00, 0x10, 0x00, 0x10, 0x00, 0x10, 0x00, 0x10, 
  0x00, 0x10, 0x00, 0x10, 0x00, 0x10, 0x00, 0x10, 0x00, 0x10, 0x00, 0x10, 0x00, 0x10, 0x00, 0x10
};

// ------------------ end generated bitmaps from image2cpp ---------------------------------



void setup() {
  // initialize serial port at 9600 bauds
  Serial.begin(9600);

  // initialize screen
  // SSD1306_SWITCHCAPVCC to generate internally 3.3V to power the display 
  // or SSD1306_EXTERNALVCC to power it externally
  if (!display.begin(SSD1306_SWITCHCAPVCC, SCREEN_ADDRESS)) {
    Serial.println(F("SSD1306 allocation failed"));
    for (;;); // Loop forever
  };



}
void loop() {
    int command = menuEncoder.getCommand();
  if (current_screen == MENU_SCREEN) { // MENU SCREEN

    // check encoder input for the menu screen

    switch (command) {
      case Encoder::CLICK:
        current_screen = 1; // menu items screen --> screenshots screen
        break;
      case Encoder::CLOCKWISE:
        item_selected = increment(item_selected, NUM_ITEMS);
         break;
      case Encoder::ANTICLOCKWISE:
        item_selected = decrement(item_selected, NUM_ITEMS);
        break;
      case Encoder::NONE:
        // Optionally do something when no command is detected
        break;
    }

    // refresh Menu screen
    refresh_menu();
  }
  else if (current_screen == OPTION_SCREEN) { // SELECTION SCREEN
    refresh_screen(item_selected);

    if (command == Encoder::CLICK)
      current_screen = MENU_SCREEN; // screenshots screen --> menu items screen 
  }
};

int increment(int item, int NUM_ITEMS) {
  int result = item + 1;
  if (result > NUM_ITEMS - 1) {
    result = 0;
  }
  return result;
}

int decrement(int item, int NUM_ITEMS) {
  int result = item - 1;
  if (result < 0 ) {
    result = NUM_ITEMS - 1;
  }
  return result;
}

void refresh_screen(int selection) {

  // refresh screen only at regular intervals
  if ((millis() - lastRefreshTime) > refreshDelay) {

    display.clearDisplay(); // clear screen

    display.setTextSize(2); // 1 - 7... (1: 4x8pix, 2: 8x16pix, ...)
    display.setFont();
    display.setTextColor(SSD1306_WHITE);
    display.setCursor(0, 20); // top left origin in pixels
    display.println(menu_items[item_selected]);

    display.display(); //refresh
    lastRefreshTime = millis();
  }
};
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

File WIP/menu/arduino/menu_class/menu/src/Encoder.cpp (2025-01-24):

#include "Encoder.h"
#include <Arduino.h> // This include is required for the Arduino-specific functions like pinMode, digitalRead, etc.

Encoder::Encoder(int clk, int dt, int sw) : pinCLK(clk), pinDT(dt), pinSW(sw), lastDebounceTime(0), debounceDelay(1) {
    pinMode(pinSW, INPUT_PULLUP);
    previousCLK = digitalRead(pinCLK);
    previousDT = digitalRead(pinDT);
    previousSW = digitalRead(pinSW);
}

int Encoder::getCommand() {
    int command = NONE;
    if ((millis() - lastDebounceTime) > debounceDelay) {
        int currentCLK = digitalRead(pinCLK);
        int currentDT = digitalRead(pinDT);
        int currentSW = digitalRead(pinSW);

        lastDebounceTime = millis();

        if ((previousCLK == HIGH) && (currentCLK == LOW)) {
            command = (currentDT == HIGH) ? CLOCKWISE : ANTICLOCKWISE;
        }

        if (previousSW == HIGH && currentSW == LOW) {
            command = CLICK;
        }

        previousCLK = currentCLK;
        previousDT = currentDT;
        previousSW = currentSW;
    }
    return command;
}

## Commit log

2023-10-22 Rename Bill of Materials.md to BOM.md
2023-12-10 OLED screen and base plate v2
2023-12-10 Sipeed_MaixSense_A010 RGBD camera initial commit (WIP)
2024-01-01 Add stepper motor and line sensor
2024-01-29 Ignore CAD folder. Miscellaneous old changes
    - updated .gitignore to ignore CAD folder and private info
    - commit notes on several BOM elements: line follower, steppers, inserts
    - add advice on traveling with a robot and soldering
    - update activity log
    - commit python scripts in ./code to command arduino with keyboard
    [Barrel1.stl, Ensamblaje_Base_2023.step, Link PDL-03-2P Power Door Lock Motor.stp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]
2024-02-10 Update RPi_setup.md
    instructions to install arduino
2024-02-10 Update RPi_setup.md
    Fix conflict between Braille package and serial ports for Arduino
2024-02-18 Configure RPi to manage Arduino remotely
2024-02-21 Pi camera setup
2024-02-21 Motor wiring
2024-03-10 Add insert hole size table
2024-03-17 Make sevillabot ROS2 package from manolobot_uno
    [camera.xacro, example_robot.urdf.xacro, gazebo_control.xacro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]
2024-03-17 Rename manolobot_uno as sevillabot
    [robot.urdf.xacro, ros2_control.xacro]
2024-03-31 Use /dev/serial/by_path/* addresses in ros2_control.xacro and joy_subscriber.py to prevent conflict between Arduinos
    [ros2_control.xacro]
2024-03-31 Add comments re. importance of plugging Arduinos in dedicated USB ports
    [ros2_control.xacro]
2024-03-31 Arduino code to control clamp with limit switches over gamepad
2024-04-09 Fix Cannot import 'GazeboRosPaths' when launching gazebo
    Apparently caused by keeping python scripts in /scripts folder, see
    https://github.com/ros-simulation/gazebo_ros_pkgs/issues/1050
    Move python scripts to my_scripts/ to avoid conflict
    Modify CMakeLists.txt accordingly
    [joy_subscriber.py]
2024-04-09 Add use_sim parameter to fix gazebo crashing at launch
    * modify rsp.launch.py: add a new `sim_mode` parameter when calling `robot.urdf.xacro`, make it same value as `use_sim_time`
    * modify robot.urdf.xacro: declare `sim_mode` xacro parameter with `false` as default
    * modify ros2_control.xacro: use `sim_mode` to toggle between DiffDriveArduino (real robot) and GazeboSystem (simulation). Add gaz_ros2_ctl_use_sim.yaml parameter file in call to libgazebo_ros2_control.so
    * create gaz_ros2_ctl_use_sim.yaml: set use_sim_time: true
    Changes made after comparing with articubot_one from Josh Newans.
    There seems to be a suboptimal use of 3 parameters:
    use_sim_time, sim_mode and use_ros2_control to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
    [robot.urdf.xacro, ros2_control.xacro]
2024-04-10 Add arduino code for line follower
2024-04-10 Use twist_mux to multiplex velocities from navigation and gamepad
    * Modify joystick.launch.py: remap velocities to `/cmd_vel_joy` instead of
    directly to`/diff_cont/cmd_vel_unstamped`
    * add config file twist_mux.yaml:
    - take joystick velocities from `/cmd_vel_joy`
    - take navigation velocities from `/cmd_vel`
    - combine them and publish to `/diff_cont/cmd_vel_unstamped`
2024-04-10 Add base_footprint_link and create config file for SLAM
    * modify robot_core.xacro: add base_footprint_link
    * create mapper_params_online_async.yaml SLAM parameter file
    [robot_core.xacro]
2024-04-10 Line follower code - initial commit
    * new file line_follower_publisher.py: node that listens to
    Arduino serial, and regularly publishes in /line_follower_error
    a custom message containing:
    - timestamp: int64 generated by millis() function. Represents ms
    since last restart of arduino. Warning: wraps after 49 days.
    - data: int in range 0-7000, generated by QTR's position function
    Represents distance from line centre.
    Note: error_mm = (data-3500)*9.525/1000
    * new file pid.py: node that listens to /line_follower_error
    topic, derives error_mm, time_s and dt_s from timestamp and data,
    calculates angular_z_vel using a PID,
    and publishes a Twist message to /cmd_vel_followe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
    [line_follower_publisher.py, pid.py]
2024-04-11 Change sign of error = (3500 - msg.data) * 9.525 / 1000000
    [pid.py]
2024-04-11 Change USB port for line_follower Arduino (cable too short)
    [line_follower_publisher.py]
2024-04-11 Add Arduino sketches for gun/clamp and line_follower
2024-04-11 Add Config file for vscode arduino extension
2024-04-11 Adjust PID constants
2024-04-11 Read serial from bottom_left USB port of the RPi (cable too short)
    [line_follower_publisher.py]
2024-04-12 Modify PID node to read PID parameters from a YAML file
    * modify pid.py and rename as pid_node.py: read parameters from YAML file
    * rename line_follower.yaml as line_follower_pid.yaml and update value of parameters
    * new pid.launch.py: launch file to read parameters from YAML file
    * modify CMakeLists.txt: adapt for new name of node pid_node.py
    [line_follower_pid.yaml]
2024-04-12 Add notes on reading PID gains from a parameter file
2024-04-12 Lidar launch file - initial commit
2024-04-12 Add notes on setup and quick start for lidar
2024-04-13 Minor improvements in notes for charging battery
2024-04-13 Reassign USB ports and update device addresses for Base and Addon arduinos after installing Mega 4 board
    [ros2_control.xacro]
2024-04-14 Add table with new device addresses when using Mega4
2024-04-14 Add components to BOM
2024-04-15 Change USB ports and device addresses due to chassis modification
    [ros2_control.xacro]
2024-04-15 Change PID gains due to change in distance between wheels
    [line_follower_pid.yaml]
2024-04-17 OAddalternative code to select device
2024-04-20 Improve notes on device addresses with Mega4
2024-04-20 Fix bug in response messages from Arduino
    [clamp_limit_switches.ino]
2024-04-20 Fix logging message when moving Clamp
    [joy_subscriber.py]
2024-04-21 Add Troubleshooting.md
    After Pi Wars 2024 bot refuse to connect to host.
    Apparently somehow the IP address assigned to the Raspberry Pi changed
    Not sure why.
    Add notes to describe step by step the recovery: find out new IP and
    update the SSH config in the host computer.
2024-06-16 Fix error: structural bars are not 300mm but 200mm
    In BOM.md fix Amazon link and title
2024-06-16 Fix price of structure kit
    Should be 17€ not 22€
2024-08-06 Add sources of CAD files
2024-08-06 Add to BOM okdo_LiDAR.md and sources
2024-08-12 Update buck converter in wiring diagram
2024-08-13 First attempt at simulating sevillabot robot
    - in robot_core.xacro:
    * add ASSY_sevillabot_base.stl mesh as visual of chassis_link
    * remove extra castor and motor links
    - in properties.xacro: modify dimensions to approximately fit sevillabot, add units for clarity
    - in camera.xacro: add camera_angle
    - in lidar.xacro: reduce min range from 0.3 to 0.1
    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
    [ADDON_castor_wheel.stl, ASSY_Wheel.stl, camera.xacro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]
2024-08-27 Improce simulation for sevillabot
    - Add .stl files in meshes folder for base, wheels, camera, lidar
    Note: .stl files correspond to version sevillabot_v1.8_animated.FCStd
    - Fine-tune .xacro files to properly render meshes, collisions,
    and inertias
    [ADDON_Lidar_assy.stl, ADDON_caster_wheel.stl, ADDON_castor_wheel.stl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]
2024-09-05 Fine tune Simulation
    * In `properties.xacro` fix bug: `W_z` (wheel axis z-offset in m) = 0.02
    (not 0.025, otherwise wheels are out of their axes!)
    Confirmed that this matches FreeCAD reference frame displacement.
    * Modify `launch_sim.launch.py`to load `sevillabot_world.world` as default
    world for gazebo simulation
    * Add default RVIZ config `display_bot.rviz`
    * In `camera.xacro`:
    - modify horizontal FOV to 160 degrees.
    - since camera is small, remove <collision> and <inertial> tags.
    * Update `Camera.md` with camera properties
    * In `Simulation.md` add notes for teleop with joystick and all changes above
    [camera.xacro, properties.xacro]
2024-09-07 Estimation of inertial properties - first commit
    [box_90x60x30.FCStd, box_90x60x30.stl, box_90x60x30_freecad_data.csv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]
2024-09-14 Review and complete BOM
2025-01-24 Initial commit of WIP projects: IMU, menu and zero
    [menu_RPi.fzz]
2025-06-17 Backup in dropbox large and private files
    - Move all large and private files to BKP_sevillabot
    - Create BKP_sevillabot/README.md explaining contents
    and link it from README.md
    - Upload a private backup of the following large and/or
    private files to Dropbox:
    * `Arduino/` - folder containing a backup of all local
    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
